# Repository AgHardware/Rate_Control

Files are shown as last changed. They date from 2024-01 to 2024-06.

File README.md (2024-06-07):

### [Nano RC12-2](Nano/RC12-2)
- uses a Nano (with ENC28J60 Ethernet shield) & an on-board mounted Cytron for rate control
	- either (1) [MD13S](https://www.cytron.io/p-13amp-6v-30v-dc-motor-driver) for single rate control
 	- or (1) [MD10C](https://www.cytron.io/c-motor-and-motor-driver/c-motor-driver/p-10amp-5v-30v-dc-motor-driver) for single rate control
- self assembled through-hole board, least expensive
- controls one rate
- can be connected to a relay module with another small pcb
- [OSHPARK](https://oshpark.com/shared_projects/UU8e90h9)
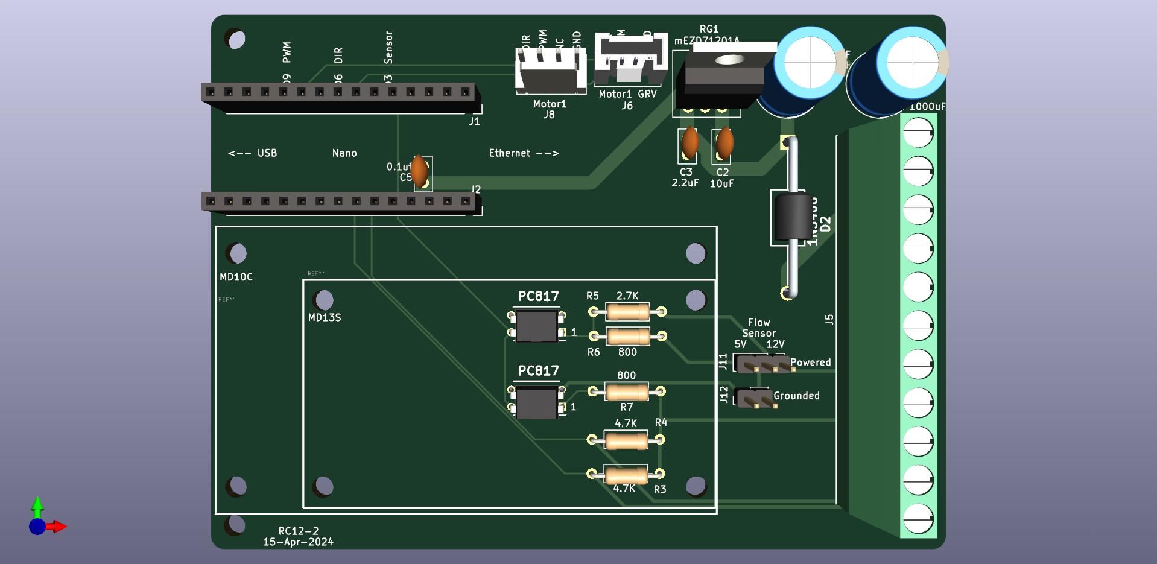
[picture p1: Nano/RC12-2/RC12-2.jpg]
Nano-RC12 photo


#
### [Teensy 4.1 RC11](Teensy/RC11_PCB)
- uses a Teensy & an on-board mounted Cytron for rate control
	- either (1) [MD13S](https://www.cytron.io/p-13amp-6v-30v-dc-motor-driver) for single rate control
 	- or (1) [MDD10A](https://www.cytron.io/p-10amp-5v-30v-dc-motor-driver-2-channels) for dual rate control
- small components are surface mount parts
- Teensy Ethernet or ESP8266 (ESP-12F) Wifi
- can control two rates and eight sections
	- 8 relays (SPST 12V output)
	- (2) 5V analog (pressure) inputs
	- (2) optically isolated digital (rate/pulse) inputs (5V)
- 5V Serial TTL header
- 3.3V I2C headers
	- supports optional external RelayDriver5 I2C board
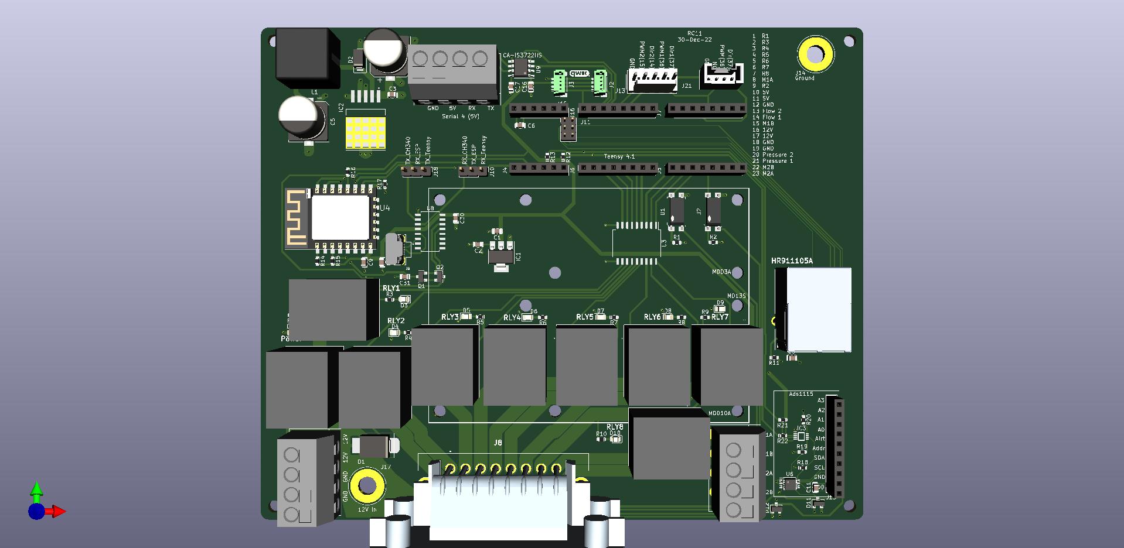
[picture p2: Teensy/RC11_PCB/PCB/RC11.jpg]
Teensy-RC11 photo


#
### [ESP32 RC15](ESP32/RC15)
- uses an ESP32 (optional W5500 Ethernet Module)
- mostly surface mount parts
- can control two rates and 7-14 sections
	- (2) DRV8870 motor drivers with reversible outputs for rates
	- (7) DRV8870 motor drivers for either 7 reversible (motorized ball valve) outputs or 14 single ended (high or low) section outputs
- (4) 5V analog inputs (or 2 differential inputs)
- (2) optically isolated digital (rate/pulse) inputs, up to 12V
- RS485 chip & header
- 3.3V I2C header
	- supports optional external RelayDriver5 I2C board
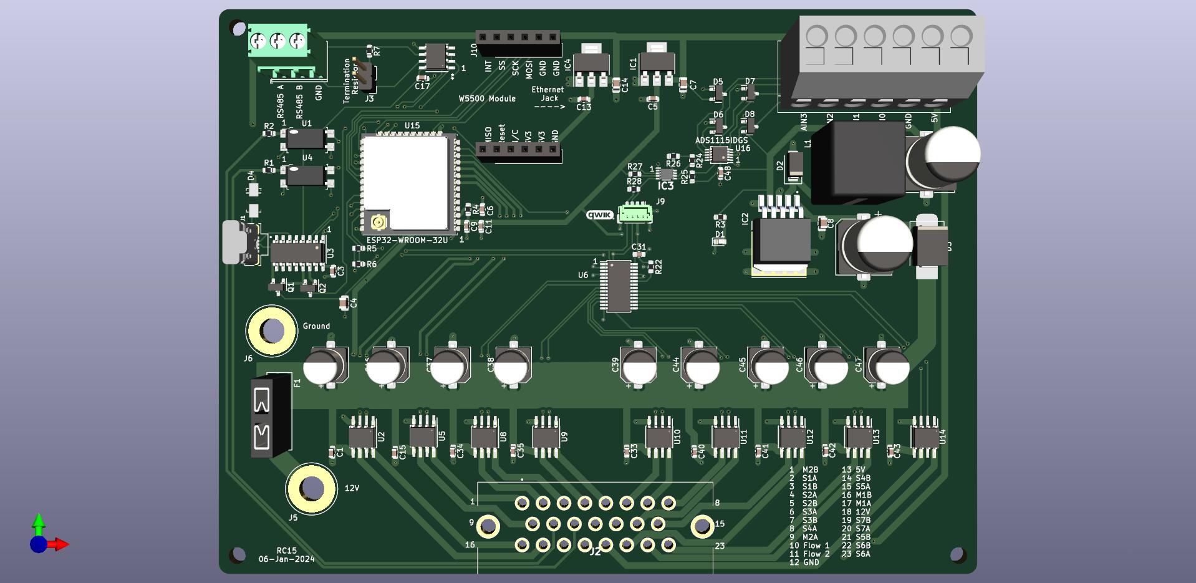
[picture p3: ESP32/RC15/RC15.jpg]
ESP32-RC15


#
### [RelayDriver5](RelayDriver5)
- PCA9535 based I2C IO expander
- designed to plug into 8 or 16 channel relay board with Qwiic cable
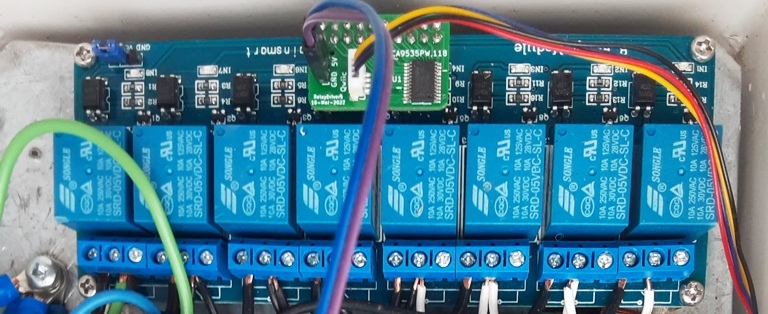
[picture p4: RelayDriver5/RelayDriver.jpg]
RelayDriver5 photo


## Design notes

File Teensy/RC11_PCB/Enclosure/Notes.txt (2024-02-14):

M3 brass nuts:

https://www.amazon.ca/Knurled-Threaded-Embedment-Printing-Projects/dp/B0BMVHYGWM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

Sealing cord:

https://www.amazon.ca/gp/product/B00R0VW4S8/ref=ppx_yo_dt_b_asin_title_o02_s00?ie=UTF8&psc=1

M3 Screws:

https://www.amazon.ca/Socket-Screws-Bolts-Thread-100pcs/dp/B07CMSBQ11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

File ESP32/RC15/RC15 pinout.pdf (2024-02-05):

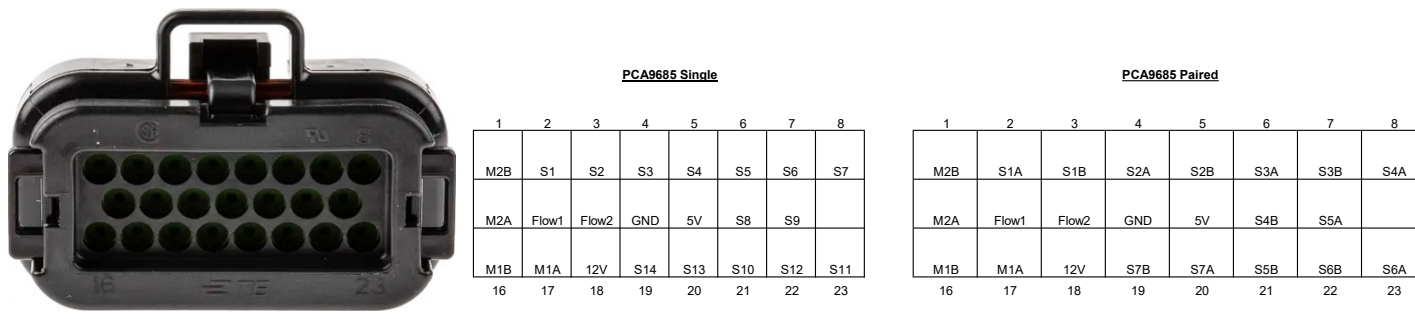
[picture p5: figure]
Flow1; Flow2; GND; PCA9685 Single; PCA9685 Paired

Ampseal 770680-1 | M2B - Motor 2 B, B connection on rate valve motor | S1A - Section 1 A, A connection on section valve motor
| Flow1 - flow/rpm sensor 1. Up to 12V. | S1B - Section 1 B, B connection on section valve motor
| S1 - Section 1
| Max peak amps: 3.6

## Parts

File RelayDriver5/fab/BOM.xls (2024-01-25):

ID | Name | Designator | Footprint | Quantity | JLCPCB Part #
1 | C145961 | J1 | Qwiic_vertical | 1 | C145961
4 | PCA9535PW,118 | U1 | MyFootprints:SOP65P640X110-24N | 1 | C255606

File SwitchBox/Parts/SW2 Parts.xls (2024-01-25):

Description | Quantity | Part Number | Unit Price | Total | location
on/off switch | 5 | M2011SS1W03 | $6.21 | $31.05 | https://www.mouser.ca/ProductDetail/NKK-Switches/M2011SS1W03?qs=sGAEpiMZZMvudeGI7i40XOVezHpYSFdNIgSw9thGWMA%3D
on/off/on switch, mometary | 2 | M2018SS1W03 | $7.19 | $14.38 | https://www.mouser.ca/ProductDetail/NKK-Switches/M2018SS1W03
enclosure |  |  |  |  | https://www.amazon.ca/Waterproof-Electrical-Electronic-Enclosure-4-53x3-54/dp/B089K9ZSBC

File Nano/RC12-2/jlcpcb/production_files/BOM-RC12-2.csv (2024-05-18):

Comment | Designator | Footprint | LCSC
2.7K | R5,R6,R7 | R_Axial_DIN0207_L6.3mm_D2.5mm_P10.16mm_Horizontal | C119333
4.7K | R3,R4 | R_Axial_DIN0207_L6.3mm_D2.5mm_P10.16mm_Horizontal | C119339
10uF | C2 | C_Disc_D5.0mm_W2.5mm_P2.50mm | C2761733
Screw_Terminal_01x11 | J5 | TerminalBlock_Phoenix_MKDS-1,5-11_1x11_P5.00mm_Horizontal | C2802625
Conn_01x15_Female | J1,J2 | PinSocket_1x15_P2.54mm_Vertical | C2932676
PC817 | U2,U3 | PC817 | C390734
Motor1 GRV | J6 | Grove | C403774
Grounded | J12 | PinHeader_1x02_P2.54mm_Vertical | C492401
Powered | J11 | PinHeader_1x03_P2.54mm_Vertical | C49257
1000uF | C1,C4 | CP_Radial_D10.0mm_P5.00mm | C503217
2.2uF | C3 | C_Disc_D5.0mm_W2.5mm_P2.50mm | C5181476
0.1uf | C5 | C_Disc_D5.0mm_W2.5mm_P2.50mm | C5632430
1N5408 | D2 | 1N5408 | C698639
Motor1 | J8 | Molex_KK-254_AE-6410-04A_1x04_P2.54mm_Vertical | C86504
mEZD71201A | RG1 | mEZD71201A

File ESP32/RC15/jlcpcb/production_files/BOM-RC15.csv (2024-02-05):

Comment | Designator | Footprint | LCSC
200K | R26 | R_0603_1608Metric | C105574
2.7K | R1,R2 | R_0603_1608Metric | C13167
0.1uF | C1,C15,C17,C3,C31,C33,C34,C35,C40,C41,C42,C43,C48,C6,C9 | C_0603_1608Metric | C14663
10uF | C14,C7 | C_0805_2012Metric | C15850
I2C | J9 | Qwic_vertical | C160390
S10MC | D3 | D_SMC_larger_pads | C169472
120 | R7 | R_0603_1608Metric | C22787
500 | R3 | R_0603_1608Metric | C22808
341 | R24,R25 | R_0603_1608Metric | C23138
BAV99 | D5,D6,D7,D8 | SOT-23 | C2500
BSS138 | Q1,Q2 | SOT-23 | C255592
10K | R22,R4 | R_0603_1608Metric | C25804
217 | R27,R28 | R_0603_1608Metric | C25811
PCA9685PW | U6 | TSSOP-28_4.4x9.7mm_P0.65mm | C2678753
1uF | C4,C8 | C_0805_2012Metric | C28323
47uF | C16,C2,C37,C38,C39,C44,C45,C46,C47 | CP_Elec_6.3x5.4 | C2836440
SS36 | D2 | SMA(DO-214AC) | C2903825
330uF | C12 | CP_Elec_10x10.5 | C3032175
470uF | C10 | CP_Elec_10x10.5 | C310845
PCA9306DCUR | IC3 | PCA9306DCUR | C33196
ADS1115IDGS | U16 | TSSOP-10_3x3mm_P0.5mm | C37593
776087-1-776087-1 | J2 | 7760871 | C378893
Conn_01x06_Socket | J10,J7 | PinSocket_1x06_P2.54mm_Vertical | C40877
2.2K | R5,R6 | R_0603_1608Metric | C4190
KF142V-5.0-6P | KF3 | KF142V-5.08-6P | C475138
C492610 | F1 | Fuse_Holder_C492610 | C492610
Screw_Terminal_01x03 | J8 | TerminalBlock_Phoenix_PT-1,5-3-5.0-H_1x03_P5.00mm_Horizontal | C5188441
105133-0011 | J1 | MOLEX_105133-0011 | C586226
22uF | C11,C13,C5 | C_0603_1608Metric | C59461
PC817 chip | U1,U4 | SMD-4_4.6x7.62mm_P2.54mm | C66405
ESP32-WROOM-32U | U15 | XCVR_ESP32-WROOM-32U | C701344
XL2596 | IC2 | TO263-5L | C74190
Conn_01x02_Pin | J3 | PinHeader_1x02_P2.54mm_Vertical | C7494857
LED | D1 | LED_0603_1608Metric | C84263
CH340C | U3 | SOIC-16_3.9x9.9mm_P1.27mm | C84681
DRV8870DDA | U10,U11,U12,U13,U14,U2,U5,U8,U9 | Texas_HTSOP-8-1EP_3.9x4.9mm_P1.27mm_EP2.95x4.9mm_Mask2.4x3.1mm_ThermalVias | C86590
AZ1117 | IC1,IC4 | SOT-223 | C92102
SMDRI127-330MT | L1 | TMPA1265SP-101MN-D | C9400
M7 - C95872 | D4 | DO-214AC | C95872
C9943 | U7 | 21-0041B_8_MXM | C9943
12V | J5 | PowerPin
Ground | J6 | PowerPin

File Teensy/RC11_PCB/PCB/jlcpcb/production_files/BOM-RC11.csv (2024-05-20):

Comment | Designator | Footprint | LCSC
SS36 | D2 | SMA(DO-214AC) | C116712
HR911105A | J12 | HR911105A | C12074
10uF | C2,C7 | C_0805_2012Metric | C15850
I2C-3V3 | J2,J3 | Qwic_vertical | C160390
S10MC | D1 | D_SMC_larger_pads | C169472
150 | R11 | R_0603_1608Metric | C22808
217 | R21,R22 | R_0603_1608Metric | C22962
341 | R18,R19 | R_0603_1608Metric | C23144
500 | R10,R23,R3,R4,R5,R6,R7,R8,R9 | R_0603_1608Metric | C23193
BAV99 | D11,D12 | SOT-23 | C2500
BSS138 | Q1,Q2 | SOT-23 | C255592
10K | R14,R15,R16,R17 | R_0603_1608Metric | C25804
200K | R20 | R_0603_1608Metric | C25811
Conn_01x08_Female | J16,J5,J6,J7 | PinSocket_1x08_P2.54mm_Vertical | C27438
1uF | C3,C31 | C_0805_2012Metric | C28323
ADS1115 - 1001001 | J19 | PinSocket_1x10_P2.54mm_Vertical | C2897373
HF3FF_012-1HST_257_ | RLY1,RLY2,RLY3,RLY4,RLY5,RLY6,RLY7,RLY8,RLY9 | HF3FF0121HST257 | C329296
PCA9306DCUR | IC3 | PCA9306DCUR | C33196
ADS1115IDGS - 1001000 | U6 | TSSOP-10_3x3mm_P0.5mm | C37593
776087-1 | J8 | 7760871 | C378893
Motor1 GRV | J21 | Grove | C403774
Conn_01x06_Female | J15,J4 | PinSocket_1x06_P2.54mm_Vertical | C40877
2.2K | R12,R13 | R_0603_1608Metric | C4190
CA-IS3722HS | U9 | SOIC-8_3.9x4.9mm_P1.27mm | C428879
KF142V-5.0-4P | KF1,KF2,KF3 | KF142V-5.08-4P | C475136
Conn_01x03_Male | J10,J18 | PinHeader_1x03_P2.54mm_Vertical | C49257
0.1uF | C11,C16,C17,C30,C6,C8,C9 | C_0805_2012Metric | C49678
105133-0011 | J9 | MOLEX_105133-0011 | C586226
22uF | C1 | C_0805_2012Metric | C602037
PC817 | U1,U2 | SMD-4_4.6x7.62mm_P2.54mm | C66405
Teensy_Ethernet | J11 | PinHeader_2x03_P2.00mm_Vertical | C6694888
330uF | C5 | CP_Elec_10x10.5 | C72510
470uF | C4 | CP_Elec_10x10.5 | C72519
XL2596 | IC2 | TO263-5L | C74190
200 | R1,R2 | R_0603_1608Metric | C8218
ESP-12F | U4 | ESP-12F | C82891
LED | D10,D13,D3,D4,D5,D6,D7,D8,D9 | LED_0805_2012Metric | C84256
ULN2803A | U3 | SOP-18_7x12.5mm_P1.27mm | C845537
CH340C | U8 | SOP-16_4.55x10.3mm_P1.27mm | C84681
Conn_01x05 | J13 | Molex_KK-254_AE-6410-05A_1x05_P2.54mm_Vertical | C86505
AZ1117 | IC1 | SOT-223 | C92517
SMDRI127-330MT | L1 | TMPA1265SP-101MN-D | C9400
Ground | J14 | PowerPin
12V In | J17 | PowerPin

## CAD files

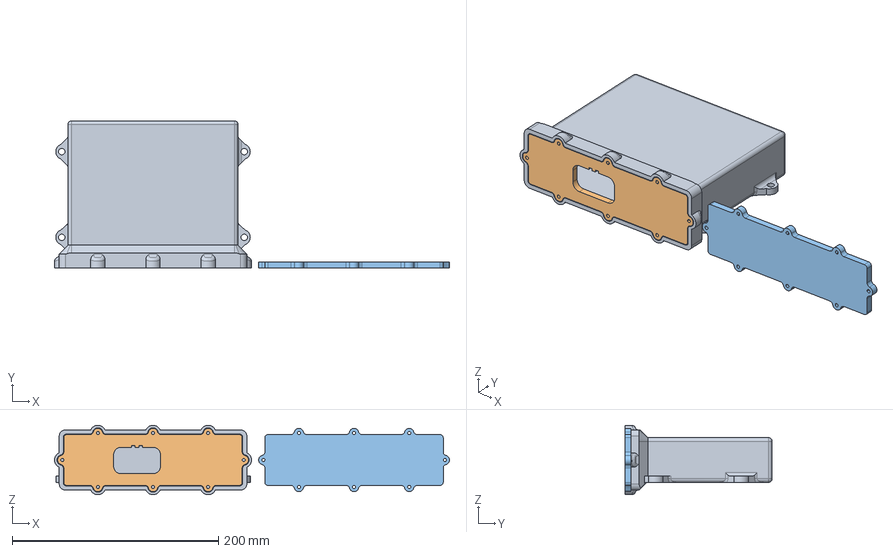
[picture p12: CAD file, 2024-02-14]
Teensy/RC11_PCB/Enclosure/RC11 box v7.step
383.1 x 143.0 x 67.4 mm

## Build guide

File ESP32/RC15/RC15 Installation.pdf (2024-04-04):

### 1. upload RC_ESP32 firmware with a usb cable. Subsequent updates can be uploaded

over wifi. In a browser enter "192.168.200.1" to get to the web interface for module 0. Module 1 would be 192.168.201.1, etc. Then select ‘Update Firmware’.

### 2. To connect to a wifi network go to the web interface/Network. Enter the network

configuration. The ESP32 will restart and attempt to connect. After 10 unsuccessful attempts it will switch to AP mode.

### 3. In AP mode the ESP32 creates a hotspot. Connect a tablet to the hotspot named

‘RateModule ( mac address)’. Use the password ‘111222333’. The rate app will need to be set to the AP subnet. This can be done on the menu/Module page of the app.

### 4. Ethernet can be used instead of wifi. A W5500 ethernet module is required. Example:

https://protosupplies.com/product/ethernet-module-w5500/

### 5. External relays can be connected with a qwiic cable and 5V power + ground using the

relay driver pcb here:
https://github.com/AgHardware/Rate_Control/tree/main/RelayDriver5 In module configurations select "PCA9555 8 relays" or "PCA9555 16 relays".

### 6. For on-board relays set module configuration to "PCA9685 single". Each pin can

control one single acting valve. The "PCA96785 paired" mode uses 2 pins to control one dual acting valve, powered on and off.

### 7. Two rates can be controlled with M1A/M1B and M2A/M2B connections to each rate

control valve. Flow1/Flow2 can use up to a 12V signal to measure flow/rpm rates.

8. Up to 4 analog sensors can be connected for pressure.

### 9. PCB connector 23 pin Ampseal 770680-1. It can be found here with wires:

https://www.ebay.ca/itm/385526456153

### 10. The ESP32 uses an IPX antenna. An example can be found here: https://universal-

solder.ca/product/2-4ghz-antenna-wi-fi-bluetooth-sma-ipx/

11. The pcb uses a mini-fuse, 10-15 amps.

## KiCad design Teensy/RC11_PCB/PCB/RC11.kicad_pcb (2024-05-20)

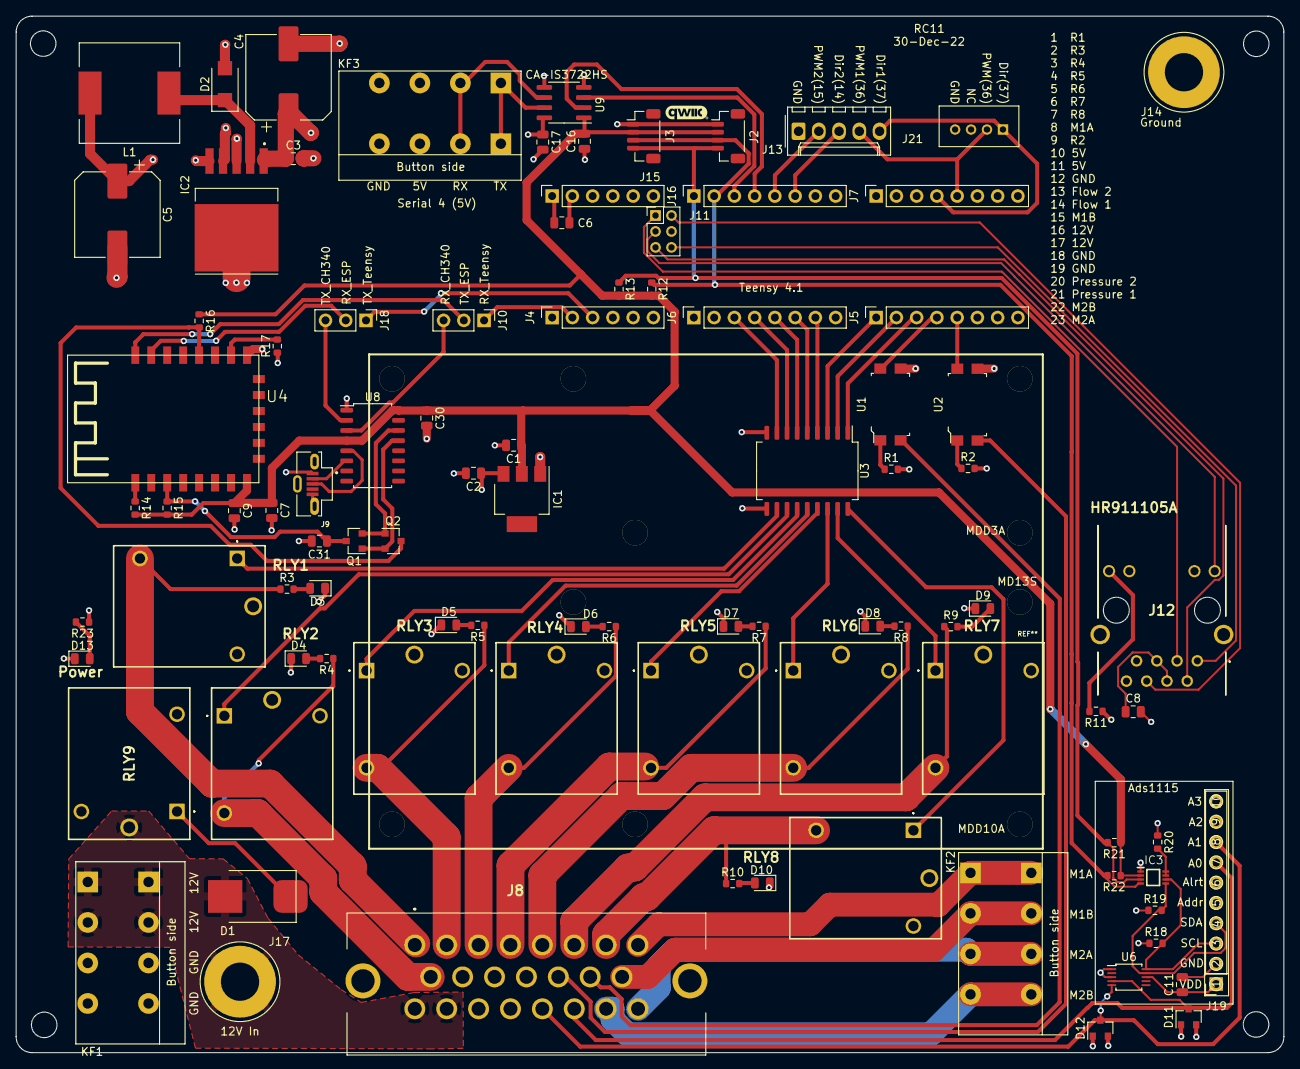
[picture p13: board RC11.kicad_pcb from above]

Board: 4 copper layers, 159.0 x 130.0 mm, 98 parts (0 on the bottom side), 86 nets.

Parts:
 : MountingHole_3.2mm_M3
 #2,  #3,  #4: MountingHole_3.2mm_M3
C1: 22uF; C_0805_2012Metric
C2, C7: 10uF; C_0805_2012Metric
C3, C31: 1uF; C_0805_2012Metric
C4: 470uF; CP_Elec_10x10.5
C5: 330uF; CP_Elec_10x10.5
C6, C8, C9, C11, C16, C17, C30: 0.1uF; C_0805_2012Metric
D1: S10MC; D_SMC_larger_pads
D2: SS36; SMA(DO-214AC)
D3, D4, D5, D6, D7, D8, D9, D10, D13: LED; LED_0805_2012Metric
D11, D12: BAV99; SOT-23
IC1: AZ1117; SOT-223
IC2: XL2596; TO263-5L
IC3: PCA9306DCUR
J2, J3: I2C-3V3; Qwic_vertical
J4, J15: Conn_01x06_Female; PinSocket_1x06_P2.54mm_Vertical
J5, J6, J7, J16: Conn_01x08_Female; PinSocket_1x08_P2.54mm_Vertical
J8: 776087-1; 7760871
J9: 105133-0011; MOLEX_105133-0011
J10, J18: Conn_01x03_Male; PinHeader_1x03_P2.54mm_Vertical
J11: Teensy_Ethernet; PinHeader_2x03_P2.00mm_Vertical
J12: HR911105A
J13: Conn_01x05; Molex_KK-254_AE-6410-05A_1x05_P2.54mm_Vertical
J14: Ground; PowerPin
J17: 12V In; PowerPin
J19: ADS1115 - 1001001; PinSocket_1x10_P2.54mm_Vertical
J21: Motor1 GRV; Grove
KF1, KF2: KF142V-5.0-4P; KF142V-5.08-4P
KF3: Serial 4 (5V); KF142V-5.08-4P
L1: SMDRI127-330MT; TMPA1265SP-101MN-D
Q1, Q2: BSS138; SOT-23
R1, R2: 200; R_0603_1608Metric
R3, R4, R5, R6, R7, R8, R9, R10, R23: 500; R_0603_1608Metric
R11: 150; R_0603_1608Metric
R12, R13: 2.2K; R_0603_1608Metric
R14, R15, R16, R17: 10K; R_0603_1608Metric
R18, R19: 341; R_0603_1608Metric
R20: 200K; R_0603_1608Metric
R21, R22: 217; R_0603_1608Metric
RLY1, RLY2, RLY3, RLY4, RLY5, RLY6, RLY7, RLY8, RLY9: HF3FF_012-1HST_257_; HF3FF0121HST257
U1, U2: PC817; SMD-4_4.6x7.62mm_P2.54mm
U3: ULN2803A; SOP-18_7x12.5mm_P1.27mm
U4: ESP-12F
U6: ADS1115IDGS - 1001000; TSSOP-10_3x3mm_P0.5mm
U8: CH340C; SOP-16_4.55x10.3mm_P1.27mm
U9: CA-IS3722HS; SOIC-8_3.9x4.9mm_P1.27mm

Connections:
12V_In: D1.2, J8.16, J8.17, J17.1, KF1.1, KF1.2, RLY9.2
+3V3: C1.1, C7.1, C9.1, C16.2, C30.1, IC1.2, IC3.2, J2.2, J3.2, R12.2, R13.2, R14.2, R15.2, R16.1, R21.1, R22.1, U4.8, U8.4, U8.16, U9.1
+5V: C2.1, C5.1, C6.1, C11.1, C17.1, D11.2, D12.2, IC1.3, IC2.4, J8.10, J8.11, J9.1, J15.1, J19.1, J19.5, KF3.3, L1.2, R1.2, R2.2, R11.1, R18.1, R19.1, R20.1, U6.8, U9.8
+12V: C3.1, C4.1, IC2.1, R23.1, RLY1.2, RLY1.3, RLY2.2, RLY2.3, RLY3.2, RLY3.3, RLY4.2, RLY4.3, RLY5.2, RLY5.3, RLY6.2, RLY6.3, RLY7.2, RLY7.3, RLY8.2, RLY8.3, RLY9.4, U3.10
AIN0: D11.3, J8.21, J19.7, U6.4
AIN1: D12.3, J8.20, J19.8, U6.5
EN: C31.1, Q1.3, R15.1, U4.3
FlowPin1: J5.4, U1.4
FlowPin2: J5.5, U2.4
GND: C1.2, C2.2, C3.2, C4.2, C5.2, C6.2, C7.2, C8.2, C9.2, C11.2, C16.1, C17.2, C30.2, C31.2, D2.2, D3.1, D4.1, D5.1, D6.1, D7.1, D8.1, D9.1, D10.1, D11.1, D12.1, D13.1, IC1.1, IC2.3, IC2.5, IC2.6, IC3.1, J2.1, J3.1, J4.1, J8.12, J8.18, J8.19, J9.5, J9.S1, J9.S2, J9.S3, J11.4, J12.8, J12.10, J12.11, J12.MH1, J12.MH2, J13.1, J14.1, J15.2, J16.8, J19.2, J21.4, KF1.3, KF1.4, KF3.4, R17.1, RLY9.3, U1.3, U2.3, U3.9, U4.15, U6.1, U6.3, U8.1, U9.4, U9.5
IO0: Q2.3, R16.2, U4.18
IO14: J13.3, J16.6
IO15: J13.2, J16.5
IO36: J7.5, J13.4, J21.2
IO37: J7.4, J13.5, J21.1
unnamed: C8.1, J12.4, J12.5
unnamed: D1.1, RLY9.1
unnamed: D2.1, IC2.2, L1.1
unnamed: D3.2, R3.2
unnamed: D4.2, R4.2
unnamed: D5.2, R5.2
unnamed: D6.2, R6.2
unnamed: D7.2, R7.2
unnamed: D8.2, R8.2
unnamed: D9.2, R9.2
unnamed: D10.2, R10.2
unnamed: D13.2, R23.2
unnamed: IC3.5, J19.4, R19.2, U6.9
unnamed: IC3.6, J19.3, R18.2, U6.10
unnamed: IC3.7, IC3.8, R20.2
unnamed: J8.8, KF2.1
unnamed: J8.15, KF2.2
unnamed: J8.22, KF2.4
unnamed: J8.23, KF2.3
unnamed: J9.2, U8.6
unnamed: J9.3, U8.5
unnamed: J11.1, J12.3
unnamed: J11.2, J12.6
unnamed: J11.3, J12.9
unnamed: J11.5, J12.2
unnamed: J11.6, J12.1
unnamed: J12.12, R11.2
unnamed: KF3.1, U9.7
unnamed: KF3.2, U9.6
unnamed: Q1.1, Q2.2, U8.13
unnamed: Q1.2, Q2.1, U8.14
unnamed: R1.1, U1.1
unnamed: R2.1, U2.1
unnamed: R14.1, U4.1
unnamed: R17.2, U4.16
unnamed: RLY1.1, U3.11
unnamed: RLY2.1, U3.12
unnamed: RLY3.1, U3.13
unnamed: RLY4.1, U3.14
unnamed: RLY5.1, U3.15
unnamed: RLY6.1, U3.16
unnamed: RLY7.1, U3.17
unnamed: RLY8.1, U3.18
R1: J8.1, R3.1, RLY1.4
R2: J8.9, R4.1, RLY2.4
R3: J8.2, R5.1, RLY3.4
R4: J8.3, R6.1, RLY4.4
R5: J8.4, R7.1, RLY5.4
R6: J8.5, R8.1, RLY6.4
R7: J8.6, R9.1, RLY7.4
R8: J8.7, R10.1, RLY8.4
RLY1: J6.3, U3.8
RLY2: J6.4, U3.7
RLY3: J6.5, U3.6
RLY4: J6.6, U3.5
RLY5: J6.7, U3.4
RLY6: J5.1, U3.3
RLY7: J5.2, U3.2
RLY8: J5.3, U3.1
RX4: J16.4, U9.2
RX_CH340: J10.3, U8.3
RX_ESP: J18.2, U4.21
RX_Teensy: J4.2, J10.1
SCL_Teensy: IC3.3, J2.4, J3.4, J16.1, R13.1, R21.2
SDA_Teensy: IC3.4, J2.3, J3.3, J16.2, R12.1, R22.2
Sensor1: J8.14, U1.2
Sensor2: J8.13, U2.2
TX4: J16.3, U9.3
TX_CH340: J18.3, U8.2
TX_ESP: J10.2, U4.22
TX_Teensy: J4.3, J18.1

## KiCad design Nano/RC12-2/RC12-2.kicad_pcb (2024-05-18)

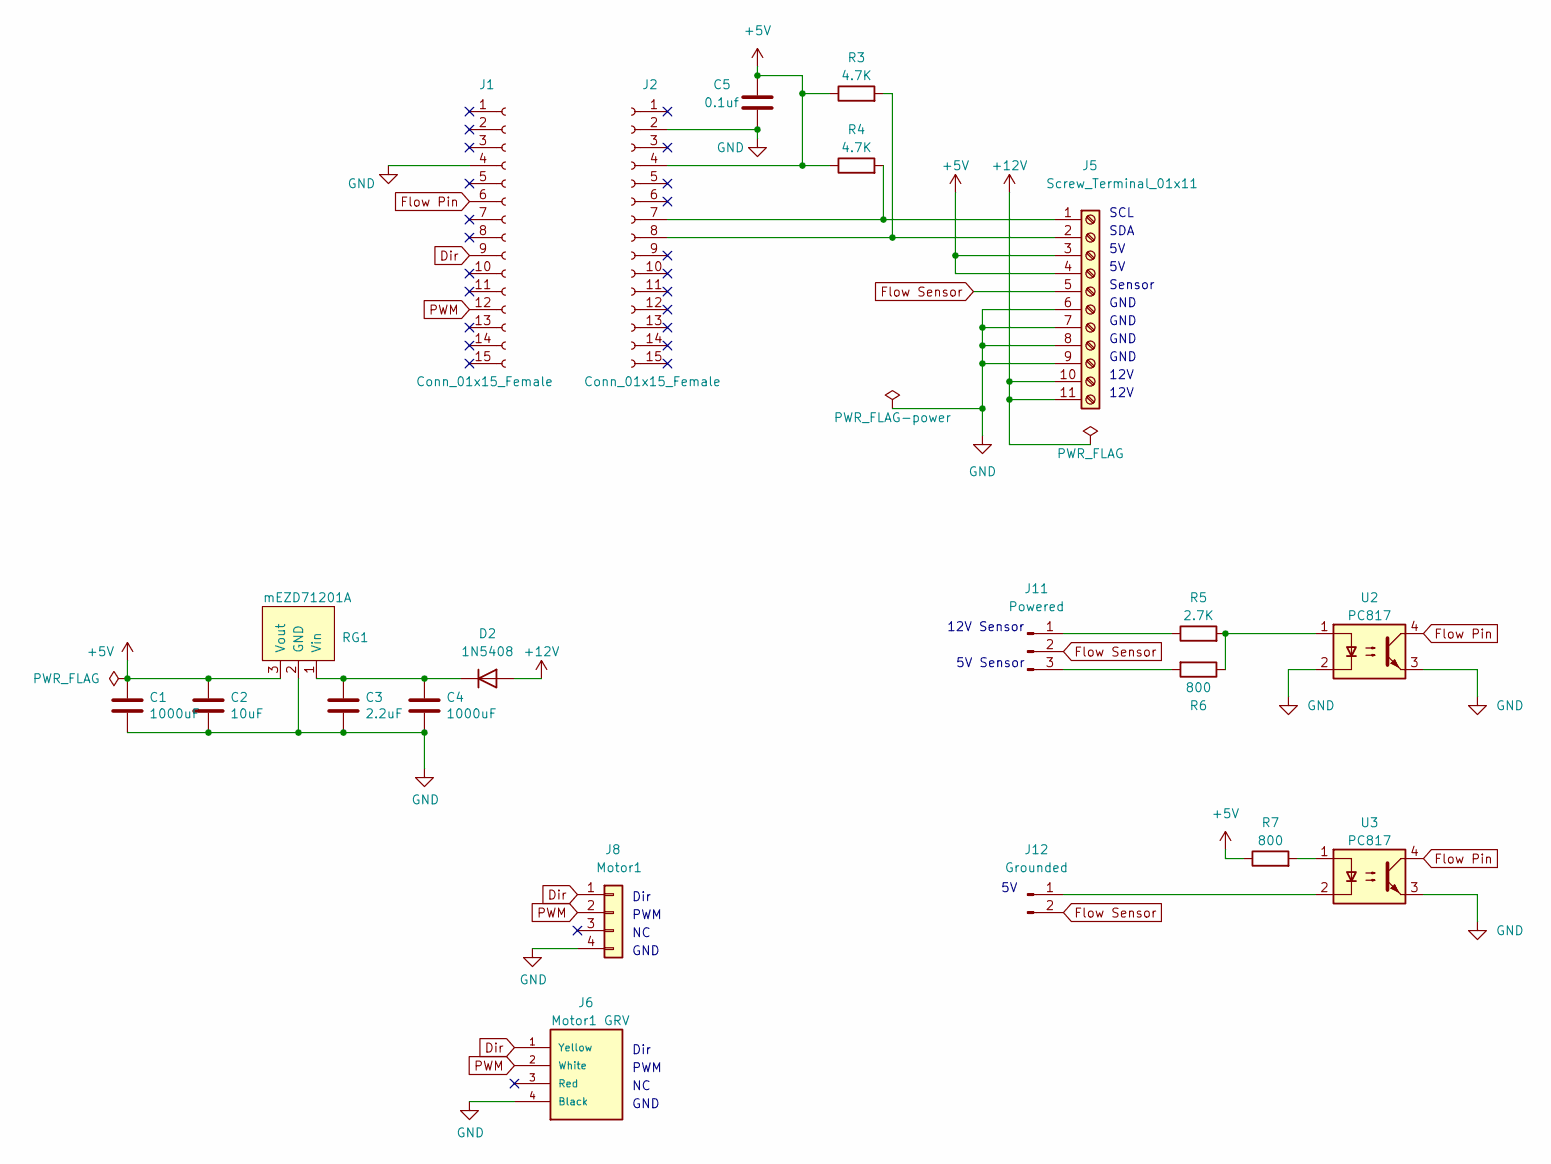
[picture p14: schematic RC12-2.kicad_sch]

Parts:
C1, C4: 1000uF; CP_Radial_D10.0mm_P5.00mm
C2: 10uF; C_Disc_D5.0mm_W2.5mm_P2.50mm
C3: 2.2uF; C_Disc_D5.0mm_W2.5mm_P2.50mm
C5: 0.1uf; C_Disc_D5.0mm_W2.5mm_P2.50mm
D2: 1N5408
J1, J2: Conn_01x15_Female; PinSocket_1x15_P2.54mm_Vertical
J5: Screw_Terminal_01x11; TerminalBlock_Phoenix_MKDS-1,5-11_1x11_P5.00mm_Horizontal
J6: Motor1 GRV; Grove
J8: Motor1; Molex_KK-254_AE-6410-04A_1x04_P2.54mm_Vertical
J11: Powered; PinHeader_1x03_P2.54mm_Vertical
J12: Grounded; PinHeader_1x02_P2.54mm_Vertical
R3, R4: 4.7K; R_Axial_DIN0207_L6.3mm_D2.5mm_P10.16mm_Horizontal
R5: 2.7K; R_Axial_DIN0207_L6.3mm_D2.5mm_P10.16mm_Horizontal
R6, R7: 800; R_Axial_DIN0207_L6.3mm_D2.5mm_P10.16mm_Horizontal
RG1: mEZD71201A
U2, U3: PC817

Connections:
+5V: C1.1, C2.1, C5.2, J2.4, J5.3, J5.4, R3.1, R4.1, R7.1, RG1.3 (Vout)
+12V: D2.2 (A), J5.10, J5.11
Dir: J1.9, J6.1 (Yellow), J8.1
Flow Pin: J1.6, U2.4, U3.4
Flow Sensor: J5.5, J11.2, J12.2
GND: C1.2, C2.2, C3.2, C4.2, C5.1, J1.4, J2.2, J5.6, J5.7, J5.8, J5.9, J6.4 (Black), J8.4, RG1.2 (GND), U2.2, U2.3, U3.3
unnamed: C3.1, C4.1, D2.1 (K), RG1.1 (Vin)
unnamed: J2.7, J5.1, R4.2
unnamed: J2.8, J5.2, R3.2
unnamed: J11.1, R5.1
unnamed: J11.3, R6.2
unnamed: J12.1, U3.2
unnamed: R5.2, R6.1, U2.1
unnamed: R7.2, U3.1
PWM: J1.12, J6.2 (White), J8.2

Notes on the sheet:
SCL
GND
SDA
5V Sensor
Dir
12V
12V Sensor
PWM
Sensor

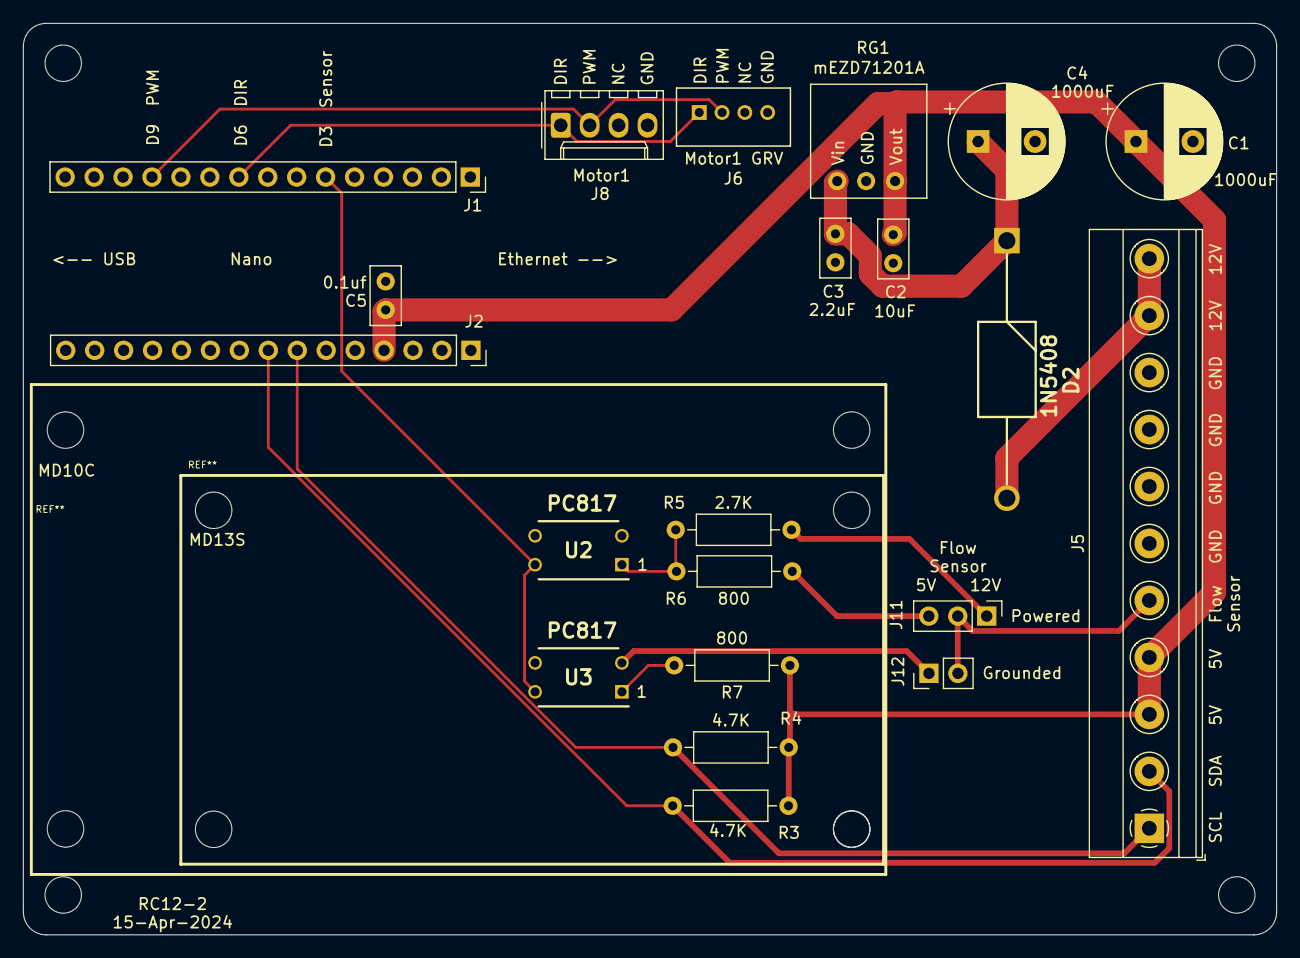
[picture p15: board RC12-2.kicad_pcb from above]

Board: 2 copper layers, 110.0 x 80.0 mm, 25 parts (0 on the bottom side), 15 nets.

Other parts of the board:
 : MountingHole_3.2mm_M3
 #2,  #3,  #4: MountingHole_3.2mm_M3

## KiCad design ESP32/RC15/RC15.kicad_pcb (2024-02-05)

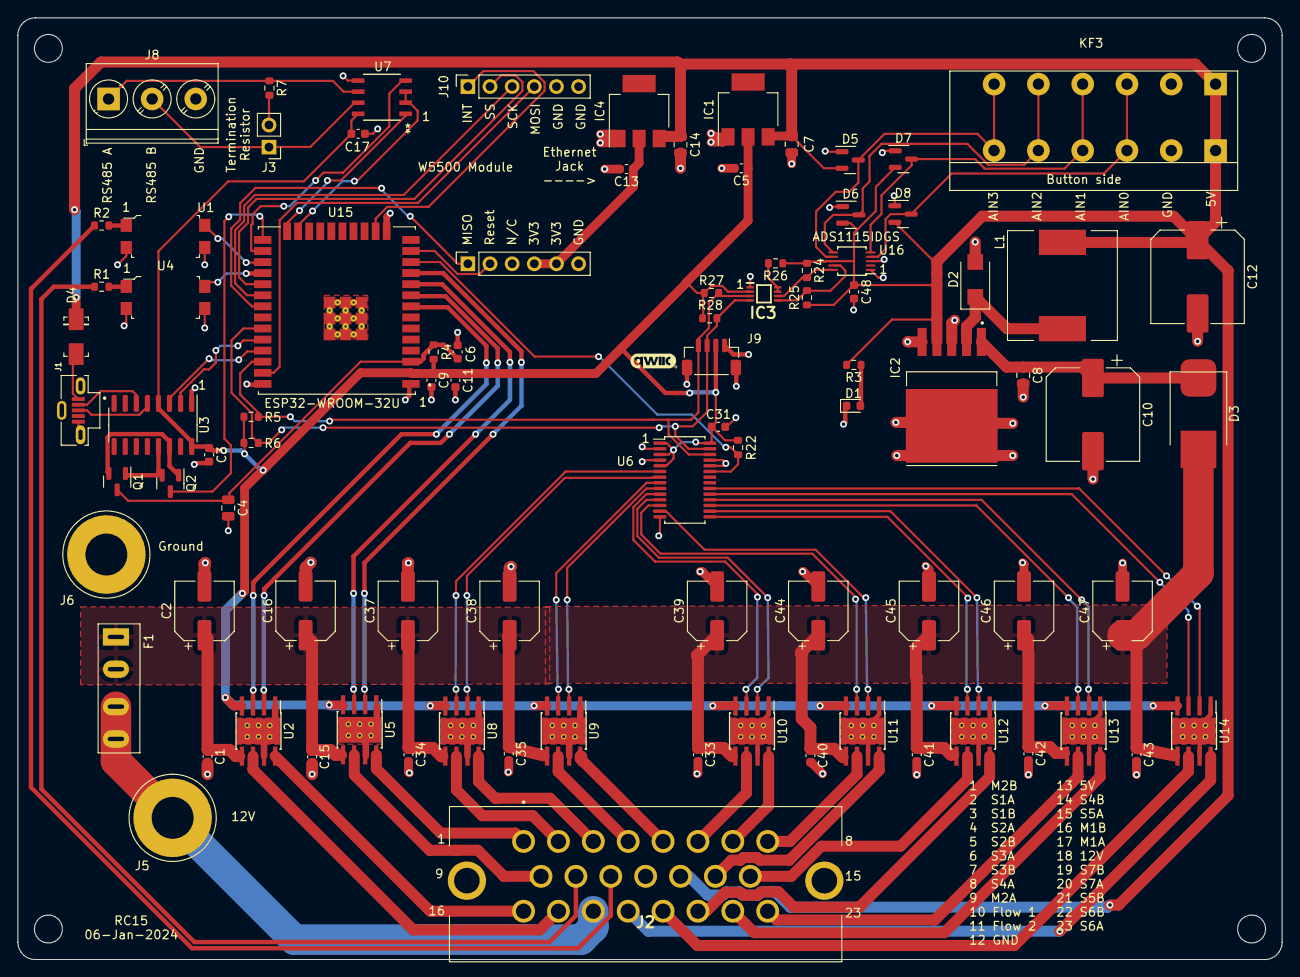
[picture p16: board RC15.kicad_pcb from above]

Board: 2 copper layers, 145.0 x 108.0 mm, 92 parts (0 on the bottom side), 82 nets.

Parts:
 : MountingHole_3.2mm_M3
 #2,  #3,  #4: MountingHole_3.2mm_M3
C1, C3, C6, C9, C15, C17, C31, C33, C34, C35, C40, C41, C42, C43, C48: 0.1uF; C_0603_1608Metric
C2, C16, C37, C38, C39, C44, C45, C46, C47: 47uF; CP_Elec_6.3x5.4
C4, C8: 1uF; C_0805_2012Metric
C5, C11, C13: 22uF; C_0603_1608Metric
C7, C14: 10uF; C_0805_2012Metric
C10: 470uF; CP_Elec_10x10.5
C12: 330uF; CP_Elec_10x10.5
D1: LED; LED_0603_1608Metric
D2: SS36; SMA(DO-214AC)
D3: S10MC; D_SMC_larger_pads
D4: M7 - C95872; DO-214AC
D5, D6, D7, D8: BAV99; SOT-23
F1: C492610; Fuse_Holder_C492610
IC1, IC4: AZ1117; SOT-223
IC2: XL2596; TO263-5L
IC3: PCA9306DCUR
J1: 105133-0011; MOLEX_105133-0011
J2: 776087-1-776087-1; 7760871
J3: Conn_01x02_Pin; PinHeader_1x02_P2.54mm_Vertical
J5: 12V; PowerPin
J6: Ground; PowerPin
J7, J10: Conn_01x06_Socket; PinSocket_1x06_P2.54mm_Vertical
J8: Screw_Terminal_01x03; TerminalBlock_Phoenix_PT-1,5-3-5.0-H_1x03_P5.00mm_Horizontal
J9: I2C; Qwic_vertical
KF3: KF142V-5.0-6P; KF142V-5.08-6P
L1: SMDRI127-330MT; TMPA1265SP-101MN-D
Q1, Q2: BSS138; SOT-23
R1, R2: 2.7K; R_0603_1608Metric
R3: 500; R_0603_1608Metric
R4, R22: 10K; R_0603_1608Metric
R5, R6: 2.2K; R_0603_1608Metric
R7: 120; R_0603_1608Metric
R24, R25: 341; R_0603_1608Metric
R26: 200K; R_0603_1608Metric
R27, R28: 217; R_0603_1608Metric
U1, U4: PC817 chip; SMD-4_4.6x7.62mm_P2.54mm
U2, U5, U8, U9, U10, U11, U12, U13, U14: DRV8870DDA; Texas_HTSOP-8-1EP_3.9x4.9mm_P1.27mm_EP2.95x4.9mm_Mask2.4x3.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
U3: CH340C; SOIC-16_3.9x9.9mm_P1.27mm
U6: PCA9685PW; TSSOP-28_4.4x9.7mm_P0.65mm
U7: C9943; 21-0041B_8_MXM
U15: ESP32-WROOM-32U; XCVR_ESP32-WROOM-32U
U16: ADS1115IDGS; TSSOP-10_3x3mm_P0.5mm

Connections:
+3.3V: C3.1, C5.1, C9.1, C11.1, C17.1, C31.1, IC1.2 (OUTPUT), IC3.2 (VREF1), J9.2, R4.1, R5.1, R6.1, R22.1, R27.1, R28.1, U2.4 (VREF), U3.4 (V3), U3.16 (VCC), U5.4 (VREF), U6.1 (A0), U6.3 (A2), U6.5 (A4), U6.28 (VDD), U7.8 (VCC), U8.4 (VREF), U9.4 (VREF), U10.4 (VREF), U11.4 (VREF), U12.4 (VREF), U13.4 (VREF), U14.4 (VREF), U15.2 (3V3)
+5V: C7.1, C12.1, C14.1, C48.1, D4.1 (K), D5.2 (A), D6.2 (A), D7.2 (A), D8.2 (A), IC1.3 (INPUT), IC2.4 (Feedback), IC4.3 (INPUT), J2.13, KF3.1, L1.2, R3.2, R24.1, R25.1, R26.1, U16.8 (VDD)
+12V: C1.1, C2.1, C15.1, C16.1, C33.1, C34.1, C35.1, C37.1, C38.1, C39.1, C40.1, C41.1, C42.1, C43.1, C44.1, C45.1, C46.1, C47.1, D3.2 (A), F1.1, U2.5 (VM), U5.5 (VM), U8.5 (VM), U9.5 (VM), U10.5 (VM), U11.5 (VM), U12.5 (VM), U13.5 (VM), U14.5 (VM)
FlowPin1: U4.4, U15.28 (IO17)
FlowPin2: U1.4, U15.27 (IO16)
FlowSensor1: J2.10, R1.1
FlowSensor2: J2.11, R2.1
GND: C1.2, C2.2, C3.2, C4.2, C5.2, C6.2, C7.2, C8.2, C9.2, C10.2, C11.2, C12.2, C13.2, C14.2, C15.2, C16.2, C17.2, C31.2, C33.2, C34.2, C35.2, C37.2, C38.2, C39.2, C40.2, C41.2, C42.2, C43.2, C44.2, C45.2, C46.2, C47.2, C48.2, D1.1 (K), D2.2, D5.1 (K), D6.1 (K), D7.1 (K), D8.1 (K), IC1.1 (ADJ/GND), IC2.3 (GND), IC2.5 (On/Off), IC2.6 (GND_1), IC3.1 (GND), IC4.1 (ADJ/GND), J1.5 (GND), J1.S1 (SHIELD), J1.S2 (SHIELD), J1.S3 (SHIELD), J2.12, J6.1, J7.6, J8.3, J9.1, J9.MP (MountPin), J10.5, J10.6, KF3.2, U1.2, U1.3, U2.1 (GND), U2.7 (ISEN), U2.9 (GND), U3.1 (GND), U4.2, U4.3, U5.1 (GND), U5.7 (ISEN), U5.9 (GND), U6.2 (A1), U6.4 (A3), U6.14 (VSS), U6.24 (A5), U6.25 (EXTCLK), U7.5 (GND), U8.1 (GND), U8.7 (ISEN), U8.9 (GND), U9.1 (GND), U9.7 (ISEN), U9.9 (GND), U10.1 (GND), U10.7 (ISEN), U10.9 (GND), U11.1 (GND), U11.7 (ISEN), U11.9 (GND), U12.1 (GND), U12.7 (ISEN), U12.9 (GND), U13.1 (GND), U13.7 (ISEN), U13.9 (GND), U14.1 (GND), U14.7 (ISEN), U14.9 (GND), U15.1 (GND), U15.15 (GND), U15.38 (GND), U15.G.1 (GND), U15.G.2 (GND), U15.G.4 (GND), U15.G.5 (GND), U15.G.6 (GND), U15.G.7 (GND), U15.G.8 (GND), U15.G.9 (GND), U15.G.10 (GND), U15.G.11 (GND), U15.G.12 (GND), U15.G.13 (GND), U15.G.14 (GND), U15.G.15 (GND), U15.G.16 (GND), U15.G.17 (GND), U15.G.18 (GND), U15.G.19 (GND), U15.G.20 (GND), U15.G.21 (GND), U15.G.22 (GND), U16.1 (ADDR), U16.3 (GND)
INTn: J10.1, U15.16 (IO13)
M1A: J2.17, U2.6 (OUT1)
M1B: J2.16, U2.8 (OUT2)
M1_IN1: U2.3 (IN1), U15.8 (I032)
M1_IN2: U2.2 (IN2), U15.9 (I033)
M2A: J2.9, U5.6 (OUT1)
M2B: J2.1, U5.8 (OUT2)
M2_IN1: U5.3 (IN1), U15.10 (I025)
M2_IN2: U5.2 (IN2), U15.11 (I026)
MISO: J7.1, U15.31 (IO19)
MOSI: J10.4, U15.37 (IO23)
unnamed: D1.2 (A), R3.1
unnamed: C8.1, C10.1, D3.1 (K), IC2.1 (VIN)
unnamed: D4.2 (A), J1.1 (VBUS)
unnamed: D2.1, IC2.2 (Output), L1.1
unnamed: IC3.7 (VREF2), IC3.8 (EN), R26.2
unnamed: IC3.6 (SCL2), R24.2, U16.10 (SCL)
unnamed: IC3.5 (SDA2), R25.2, U16.9 (SDA)
unnamed: C13.1, IC4.2 (OUTPUT), J7.4, J7.5
unnamed: J1.3 (D+), U3.5 (UD+)
unnamed: J1.2 (D-), U3.6 (UD-)
unnamed: J3.1, J8.2, U7.7 (B)
unnamed: J3.2, R7.2
unnamed: F1.2, J2.18, J5.1
unnamed: J8.1, R7.1, U7.6 (A)
unnamed: Q1.1 (G), Q2.2 (S), U3.13 (~DTR)
unnamed: Q1.2 (S), Q2.1 (G), U3.14 (~RTS)
unnamed: Q2.3 (D), U15.25 (IO0)
unnamed: R1.2, U4.1
unnamed: R2.2, U1.1
unnamed: U6.6 (LED0), U8.3 (IN1)
unnamed: U6.7 (LED1), U8.2 (IN2)
unnamed: U6.8 (LED2), U9.3 (IN1)
unnamed: U6.9 (LED3), U9.2 (IN2)
unnamed: U6.10 (LED4), U10.3 (IN1)
unnamed: U6.11 (LED5), U10.2 (IN2)
unnamed: U6.12 (LED6), U11.3 (IN1)
unnamed: U6.13 (LED7), U11.2 (IN2)
unnamed: U6.15 (LED8), U12.3 (IN1)
unnamed: U6.16 (LED9), U12.2 (IN2)
unnamed: U6.17 (LED10), U13.3 (IN1)
unnamed: U6.18 (LED11), U13.2 (IN2)
unnamed: U6.19 (LED12), U14.3 (IN1)
unnamed: U6.20 (LED13), U14.2 (IN2)
unnamed: D8.3 (K), KF3.3, U16.4 (AIN0)
unnamed: D7.3 (K), KF3.4, U16.5 (AIN1)
unnamed: D6.3 (K), KF3.5, U16.6 (AIN2)
unnamed: D5.3 (K), KF3.6, U16.7 (AIN3)
OutputEnable: R22.2, U6.23 (~OE), U15.12 (IO27)
RS485_Enable: U7.2 (~RE), U7.3 (DE), U15.23 (IO15)
RX2: U7.1 (RO), U15.24 (IO2)
ResetNW: J7.2, U15.13 (IO14)
S1A: J2.2, U8.6 (OUT1)
S1B: J2.3, U8.8 (OUT2)
S2A: J2.4, U9.6 (OUT1)
S2B: J2.5, U9.8 (OUT2)
S3A: J2.6, U10.6 (OUT1)
S3B: J2.7, U10.8 (OUT2)
S4A: J2.8, U11.6 (OUT1)
S4B: J2.14, U11.8 (OUT2)
S5A: J2.15, U12.6 (OUT1)
S5B: J2.21, U12.8 (OUT2)
S6A: J2.23, U13.6 (OUT1)
S6B: J2.22, U13.8 (OUT2)
S7A: J2.20, U14.6 (OUT1)
S7B: J2.19, U14.8 (OUT2)
SCK: J10.3, U15.30 (IO18)
SCL: IC3.3 (SCL1), J9.4, R5.2, R27.2, U6.26 (SCL), U15.36 (IO22)
SDA: IC3.4 (SDA1), J9.3, R6.2, R28.2, U6.27 (SDA), U15.33 (IO21)
SS: J10.2, U15.29 (IO5)
TX2: U7.4 (DI), U15.26 (IO4)
uC_EN: C4.1, C6.1, Q1.3 (D), R4.2, U15.3 (EN)
uC_RX: U3.2 (TXD), U15.34 (RXD0)
uC_TX: U3.3 (RXD), U15.35 (TXD0)

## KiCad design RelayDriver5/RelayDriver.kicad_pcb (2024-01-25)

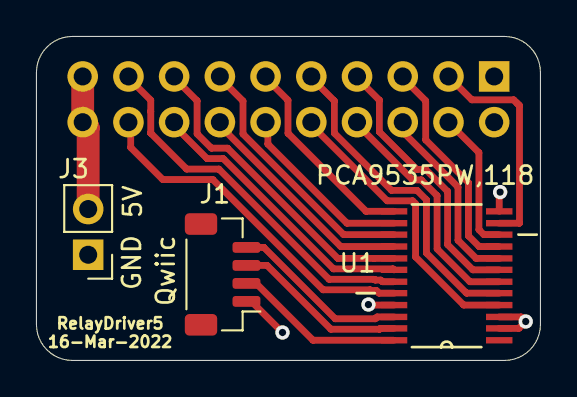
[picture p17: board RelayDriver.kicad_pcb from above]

Board: 2 copper layers, 28.0 x 18.0 mm, 4 parts (1 on the bottom side), 21 nets.

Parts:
J1: Qwiic; Qwic_vertical
J2: PinSocket_2x10_P2.54mm_Vertical
J3: PinHeader_1x02_P2.54mm_Vertical
U1: PCA9535PW,118; SOP65P640X110-24N

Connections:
GND: J1.1, J2.1, J2.2, J3.1, U1.2, U1.3, U1.12, U1.21
unnamed: J1.2, U1.24
unnamed: J1.3, U1.23
unnamed: J1.4, U1.22
unnamed: J2.3, U1.11
unnamed: J2.4, U1.10
unnamed: J2.5, U1.9
unnamed: J2.6, U1.8
unnamed: J2.7, U1.7
unnamed: J2.8, U1.6
unnamed: J2.9, U1.5
unnamed: J2.10, U1.4
unnamed: J2.11, U1.13
unnamed: J2.12, U1.14
unnamed: J2.13, U1.15
unnamed: J2.14, U1.16
unnamed: J2.15, U1.17
unnamed: J2.16, U1.18
unnamed: J2.17, U1.19
unnamed: J2.18, U1.20
unnamed: J2.19, J2.20, J3.2

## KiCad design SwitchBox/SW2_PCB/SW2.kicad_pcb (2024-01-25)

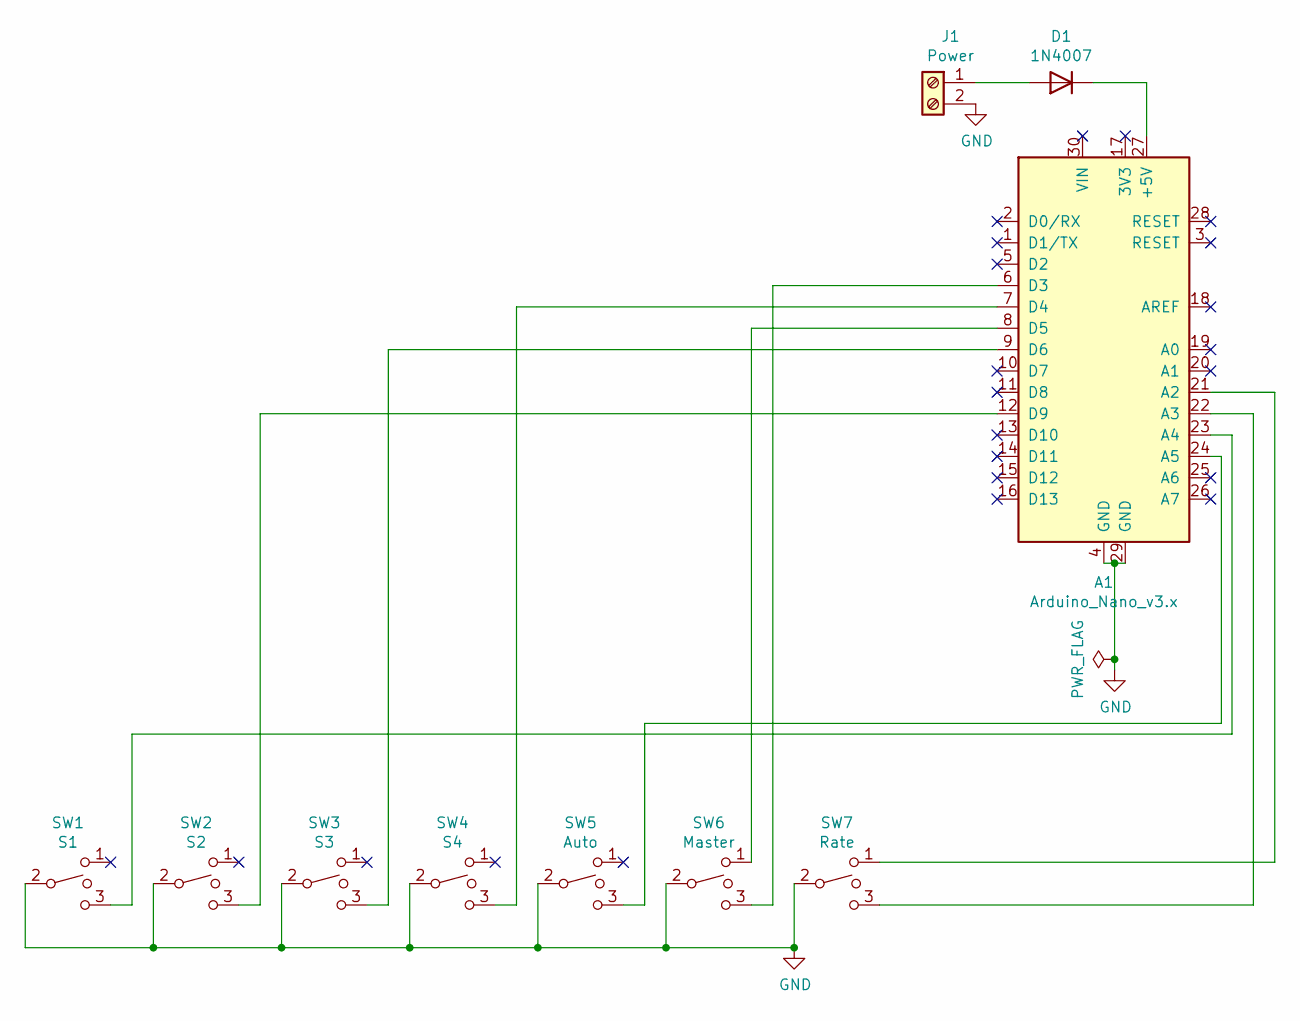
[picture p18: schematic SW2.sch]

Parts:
A1: Arduino_Nano_v3.x; Arduino_Nano
D1: 1N4007; D_DO-41_SOD81_P10.16mm_Horizontal
J1: Power; TerminalBlock_Phoenix_PT-1,5-2-5.0-H_1x02_P5.00mm_Horizontal
SW1: S1; Mini_Toggle_3pin
SW2: S2; Mini_Toggle_3pin
SW3: S3; Mini_Toggle_3pin
SW4: S4; Mini_Toggle_3pin
SW5: Auto; Mini_Toggle_3pin
SW6: Master; Mini_Toggle_3pin
SW7: Rate; Mini_Toggle_3pin

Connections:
GND: A1.4 (GND), A1.29 (GND), J1.2, SW1.2, SW2.2, SW3.2, SW4.2, SW5.2, SW6.2, SW7.2
unnamed: A1.6 (D3), SW6.3
unnamed: A1.7 (D4), SW4.3
unnamed: A1.8 (D5), SW6.1
unnamed: A1.9 (D6), SW3.3
unnamed: A1.12 (D9), SW2.3
unnamed: A1.21 (A2), SW7.1
unnamed: A1.22 (A3), SW7.3
unnamed: A1.23 (A4), SW1.3
unnamed: A1.24 (A5), SW5.3
unnamed: A1.27 (+5V), D1.1 (K)
unnamed: D1.2 (A), J1.1

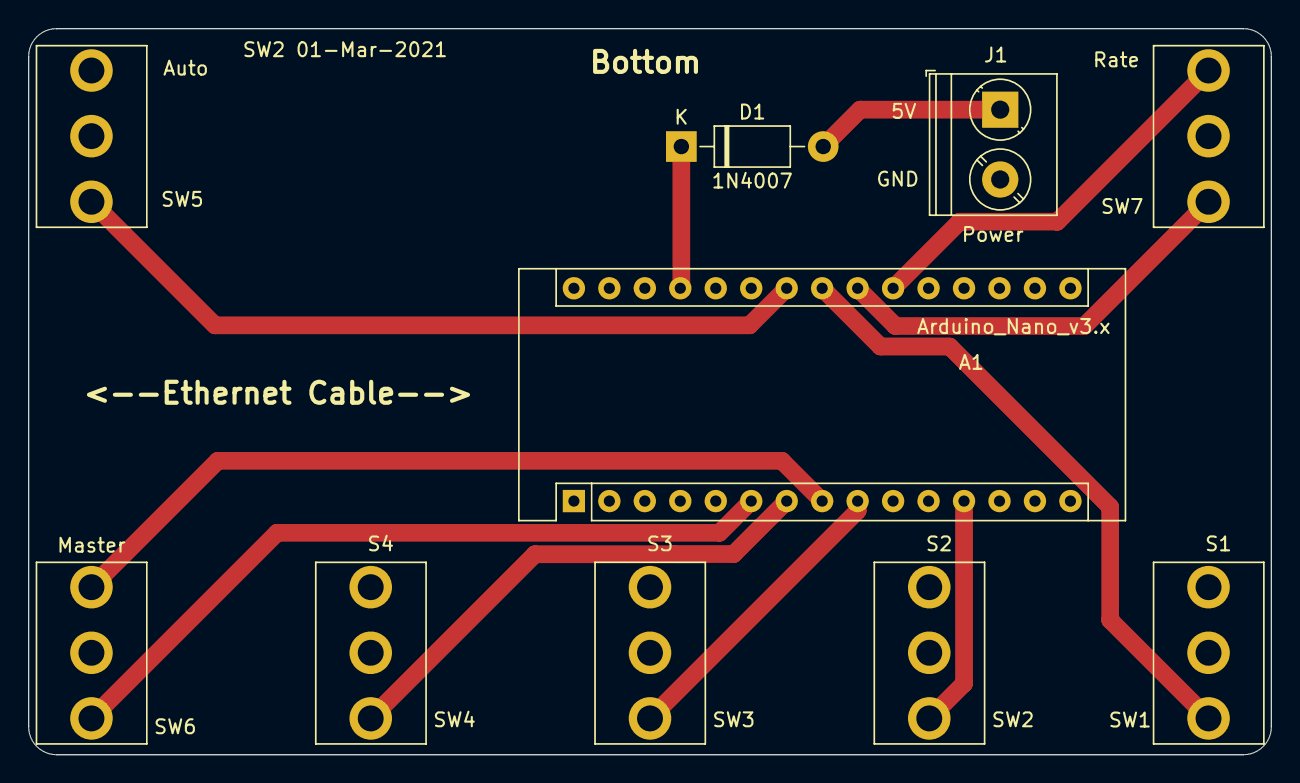
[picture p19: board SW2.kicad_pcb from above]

Board: 2 copper layers, 89.0 x 52.0 mm, 10 parts (0 on the bottom side), 12 nets.

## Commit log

2024-01-25 remove file
    [AS12-B_Cu.gbr, AS12-B_Mask.gbr, AS12-B_Paste.gbr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]
2024-01-26 Notes for diode D2
2024-02-05 add ESP32 rate board
    [Analog.kicad_sch, BOM-RC15.csv, DRVs.kicad_sch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]
2024-02-14 add RC11 enclosure
    [RC11 box v7.step]
2024-02-17 fix RC11 board image
2024-05-18 add RC12-2
    [BOM-RC12-2.csv, BOM-RC12-2.xls, BOM-RC12.csv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]
2024-05-20 update fab components
    [BOM-RC11.csv, BOM.xls, PickAndPlace_RC11_2022-12-31.csv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]
